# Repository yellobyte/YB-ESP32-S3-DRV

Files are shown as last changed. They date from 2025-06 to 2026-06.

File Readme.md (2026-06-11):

## YB-ESP32-S3-DRV Development Board Overview:
The **YB-ESP32-S3-DRV** is a development board based on Espressif's ESP32-S3 MCU and especially designed for driving a wide range of loads including **solenoids**, **stepper motors (e.g. 28BYJ-48)**, **high power LEDs**, etc. It features an **ESP32-S3-WROOM-1-N8R2** module (8MB Flash, 2MB PSRAM, WiFi PCB antenna) and is available on sales platforms [eBay](https://www.ebay.de/sch/i.html?_nkw=yb-esp32-s3) and [Ricardo.ch](https://www.ricardo.ch/en/s/YB-ESP32-S3).

Apart from the Espressif **ESP32-S3** MCU it provides a modern driver IC [Toshiba TBD62083A](https://github.com/yellobyte/YB-ESP32-S3-DRV/raw/main/doc/TBD62083A_datasheet.pdf) **8-channel sink type DMOS transistor array**  similar to an ULN2003/ULN2803 (7/8-channel Darlington array) but with 8 MOSFET output stages, **USB-C connector** for software upload, serial output and/or feeding power to the ESP32 section on the board, **two status LEDs** and **GPIO pins** for free use. The USB-C is connected directly to the ESP32-S3 to allow for serial output and JTAG debugging.

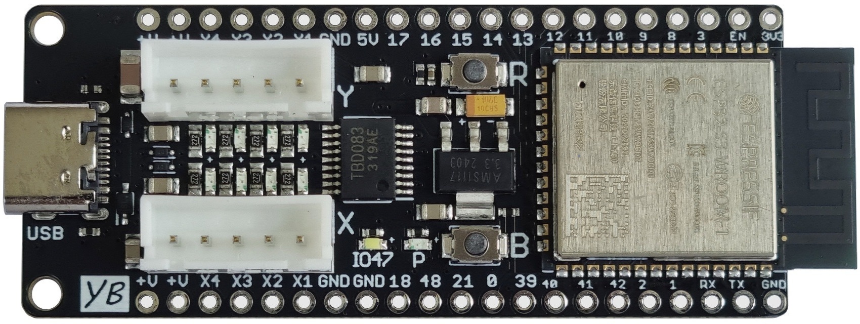
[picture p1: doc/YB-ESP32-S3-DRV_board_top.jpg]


There are plenty of GPIOs available so you can connect additional hardware to the board, e.g. TFT displays, buttons, switches, sensors, modules that communicate via I2C/SPI, etc. Please have a look at the provided [examples](https://github.com/yellobyte/YB-ESP32-S3-DRV/tree/main/examples) for PlatformIO resp. ArduinoIDE.

The densly populated 4-layer YB-ESP32-S3-DRV board is still highly [breadboard compatible](https://github.com/yellobyte/YB-ESP32-S3-DRV/raw/main/doc/YB-ESP32-S3-DRV_on_breadboard.jpg) for it leaves one row of accessible breadboard contacts on either side of the board. All I/O ports (GPIOx) are clearly labeled on both sides of the board.

### Driving inductive loads

The boards driver IC is especially suited for driving inductive loads, e.g. **solenoids** or **stepper motors**. Since a common microcontroller can only drive a few 10mA and low voltages it is commonly paired with a driver IC that can handle higher current and/or voltage levels, e.g. the very popular ULN2003/ULN2803. Such chip can drive up to 500mA current and contains suppression (flyback/freewheeling) diodes. A major disadvantage of the ULN are the darlington transistors at the output which cause a high forward voltage when switched on and therefore a considerable waste of energy. To make matters worse, the high forward voltage (Vf) of about 1.5-2V notably reduces the working voltage of a connected device.

This board features the **modern 8-channel Toshiba driver chip** with MOSFET outputs (~0.5Vf) and suppression diodes on each channel.

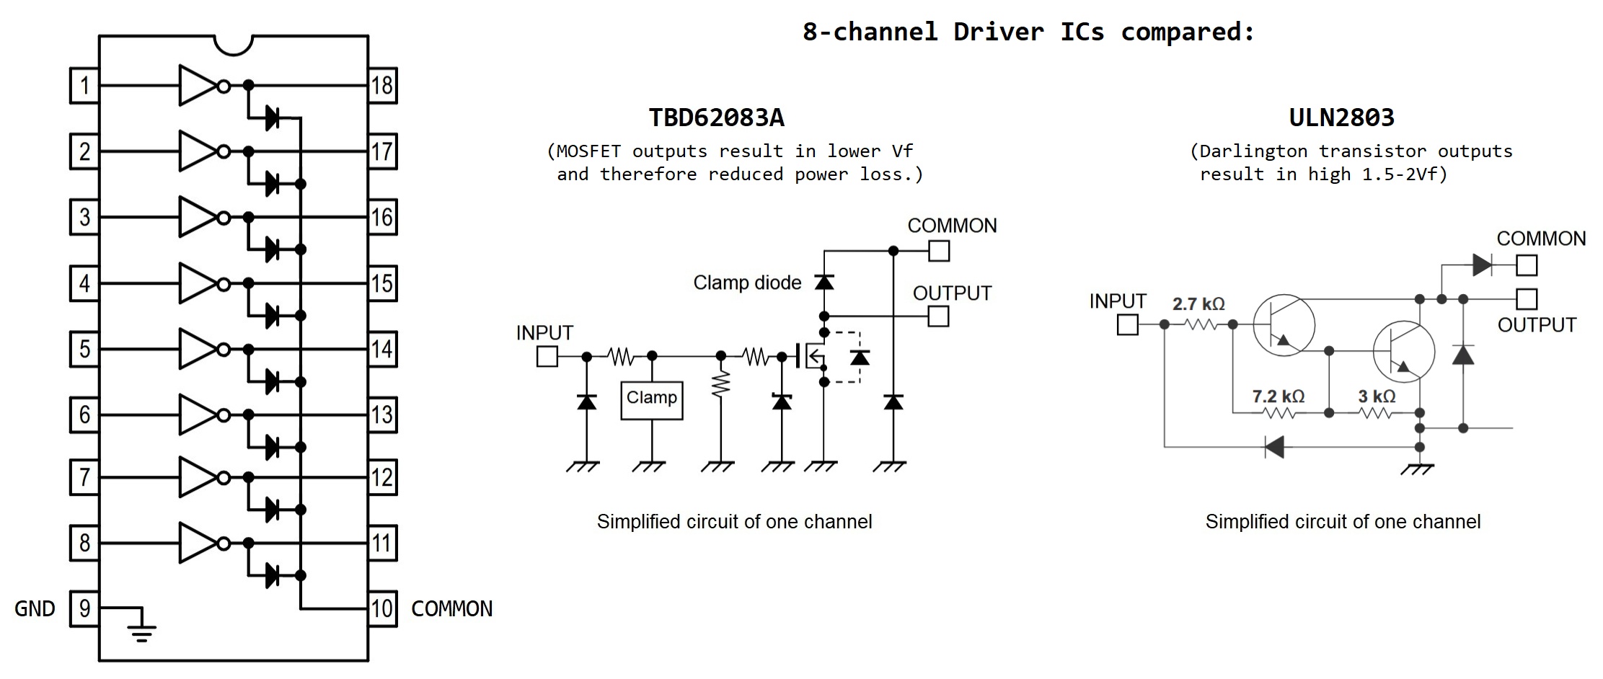
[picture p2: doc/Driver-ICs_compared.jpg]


Furthermore the board provides **two JST XH connectors** that match exactly the 5-wire connector of a common 5V/12V [**28BYJ-48 stepper motor**](https://github.com/yellobyte/YB-ESP32-S3-DRV/raw/main/doc/28BYJ-48-Stepper-Motor-Spec.pdf). This lets you easily plug two such motors into the board without the need for any extra wiring between board and steppers.

In addition, the board features **eight channel LEDs** (connected to X1...X4 and Y1...Y4) that indicate [channel activity](https://github.com/yellobyte/YB-ESP32-S3-DRV/raw/main/doc/YB-ESP32-S3-DRV_board_with_two_5V-steppers.mp4) and therefore provides a clear visual feedback as motors step or solenoids and other connected devices get activated. If you prefer them to stay dark then solder bridges LEDX/LEDY must be opened.

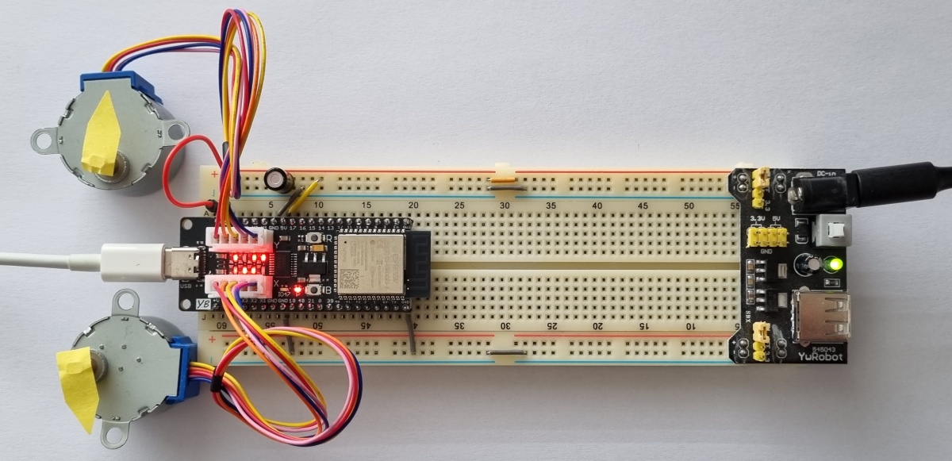
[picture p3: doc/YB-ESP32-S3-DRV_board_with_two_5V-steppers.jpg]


**Please note:**  The USB cable connected to the board in above scenario is only for data communication with a PC! The power for the two 5V stepper motors and the dev board in this case is provided by the breadboard power supply visible on the right hand side.

## YB-ESP32-S3-DRV board features in detail:
 - **ESP32-S3-WROOM-1-N8R2** module with 8MB Flash, 2MB PSRAM, WiFi PCB antenna
 - **Toshiba TBD62083A** driver IC, an 8-channel sink type DMOS transistor array with integrated suppression diodes for inductive load driving. Each channel is rated at 500mA max. output current resp. 50V max. output voltage. Outputs can be paralleled for higher current. This driver chip is similar to the commonly used ULN2803 but offers reduced forward voltage Vf at each output (when on) by using a DMOS MOSFET transistor instead of darlingtons. The chip is connected to the ESP32-S3 as follows:
   - *GPIO35...GPIO38* - for driving pins X1...X4 (additionally routed to 'X' socket)
   - *GPIO4...GPIO7* - for driving pins Y1...Y4 (additionally routed to 'Y' socket)

    Please note: The maximal power dissipation Pd of the chip must not exceed 0.96W at any time. If needed, a heat sink can be mounted on the chip. Folder [doc](https://github.com/yellobyte/YB-ESP32-S3-DRV/tree/main/doc) holds the driver IC's spec sheet.
 - **2 x JST XH connector** with 4 output channels each (connected to pins X1...X4, resp. Y1...Y4). They match exactly the 5-wire connector of a common 28BYJ-48 stepper motor.
 - **control LEDs**. One LED labeled 'P' is connected to the 3.3V rail to indicate board power and the other LED labeled 'IO47' is connected to GPIO47 which can be used as status LED.
 - **USB-C** port connected directly to the ESP32-S3 for serial output, software upload (e.g. via ArduinoIDE, VSCode/PlatformIO etc) or JTAG debugging. Can also be used to power the onboard ESP32-S3 module.

 - **Two pushbuttons**. One is labeled 'R' and resets the ESP32-S3 (shorts EN pin to ground) and the other one is labeled 'B' and shorts GPIO0 to ground when pressed. The latter is sometimes needed to force the board into boot mode.
 - **lots of available GPIOs**, useful for connecting LEDs, buttons, additional modules via SPI or I2C, e.g displays, rotary encoders, bluetooth, etc.

In summary, the board replaces a lot of separate modules & cables, saves space on a breadboard and might avoid the odd frustration to get it all running.

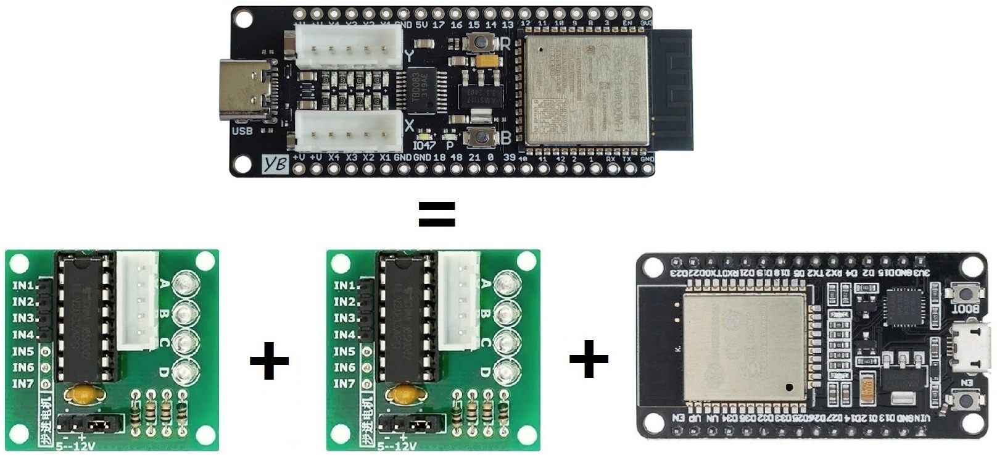
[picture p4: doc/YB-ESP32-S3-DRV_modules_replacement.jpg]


## Board Pin Layout:
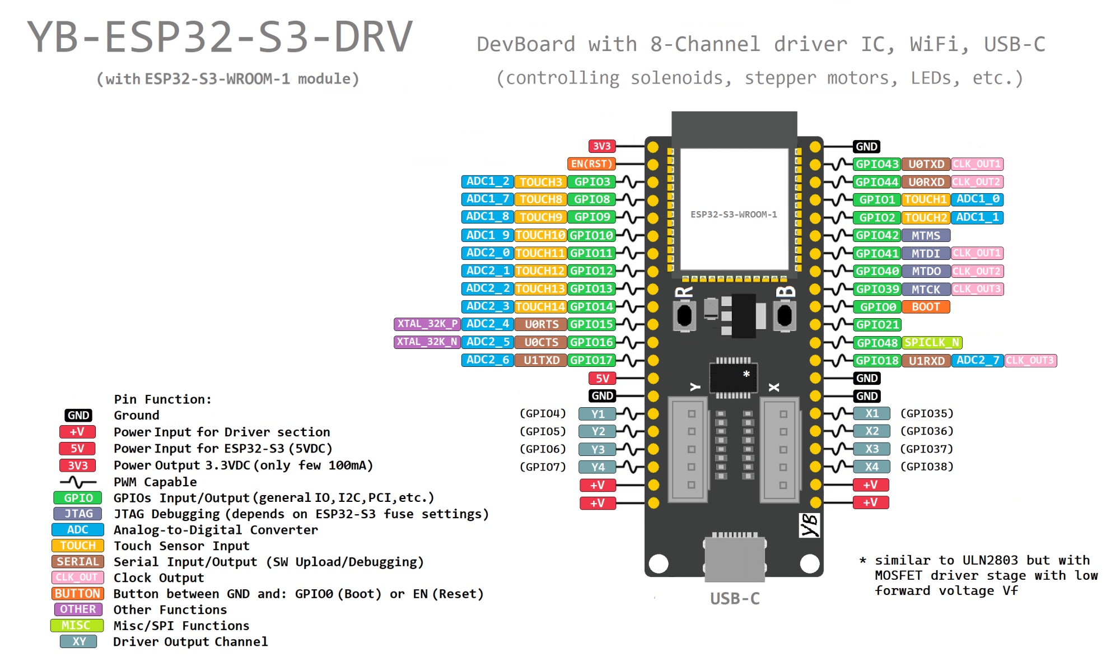
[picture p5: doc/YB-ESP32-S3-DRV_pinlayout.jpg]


The boards **pin layout**, **outline** and **schematic** files are all located in folder [doc](https://github.com/yellobyte/YB-ESP32-S3-DRV/tree/main/doc).

## Powering the board:
### ESP32 section:
There are different ways to provide power to the onboard ESP32-S3 module:
  - through the USB-C port or
  - 5VDC applied to the 5V pin

The board uses a LDO to drop the external supply voltage to 3.3Volt needed by the ESP32-S3.

### Driver section:
Board pins labeled *+V* are intended to provide power to external devices only. They are connected to pin 5 of each JST XH connector. Since all components on this +V rail (C1, C6...C9, IC1) are rated for 50Vmax you might go even higher than 12VDC if necessary.

**Important:**
You must make sure your project never exceeds the electrical and thermal limits of the driver chip IC1.

**Recommended wiring for greater loads:**
When the driver chip is supposed to carry more then just a few 10mA on each output channel than it is recommended to use a capable power supply on the +V rail and preferably an additional capacitor of 220uF or greater value across the +V/GND pins of the board as shown below:

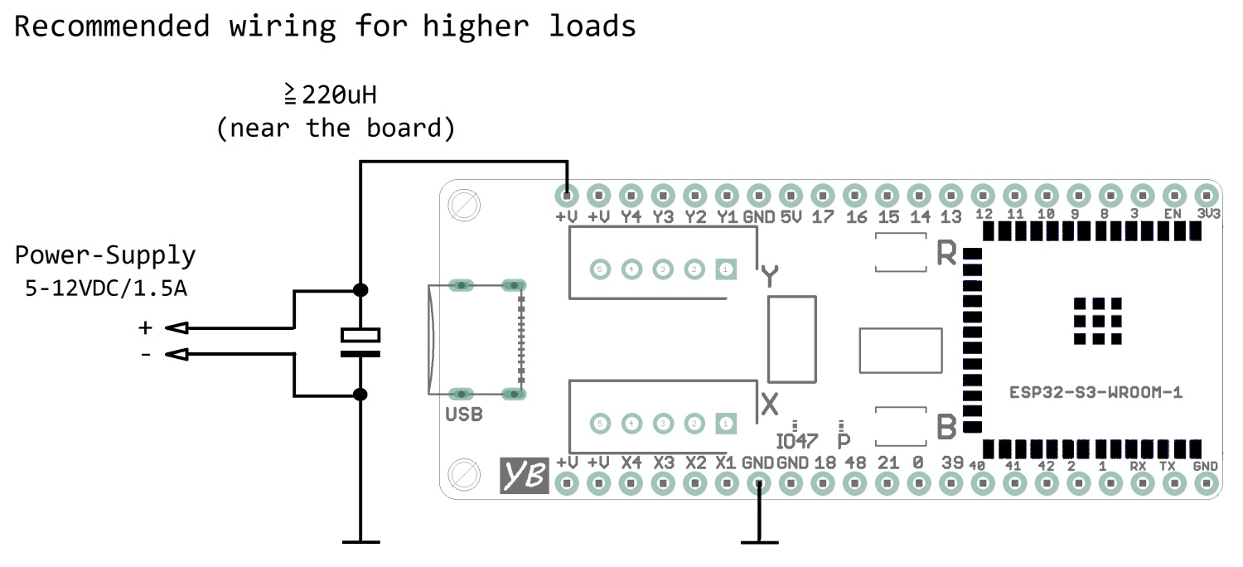
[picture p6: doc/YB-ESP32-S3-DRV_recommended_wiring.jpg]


## Application hints:

### Arduino IDE:
As of Arduino ESP32 Core V3.2.1 you open the board list, enter "yb-" and select "**Yellobyte YB-ESP32-S3-DRV**". Then choose the proper settings for COM port, debug level, flash size, PSRAM, etc. as shown below. Be aware, since the ESP32-S3 MCU is very versatile there are a lot of build options to play with. Espressif's homepage offers some help.

Correct **ArduinoIDE** settings for the **YB-ESP32-S3-DRV** board:
- Board: *YB-ESP32-S3-DRV*
- USB CDC On Boot: *Enabled*
- Flash Size: *8MB (64Mb)*
- Partition Scheme: *8MB with spiffs (...)*
- PSRAM: *QSPI PSRAM*

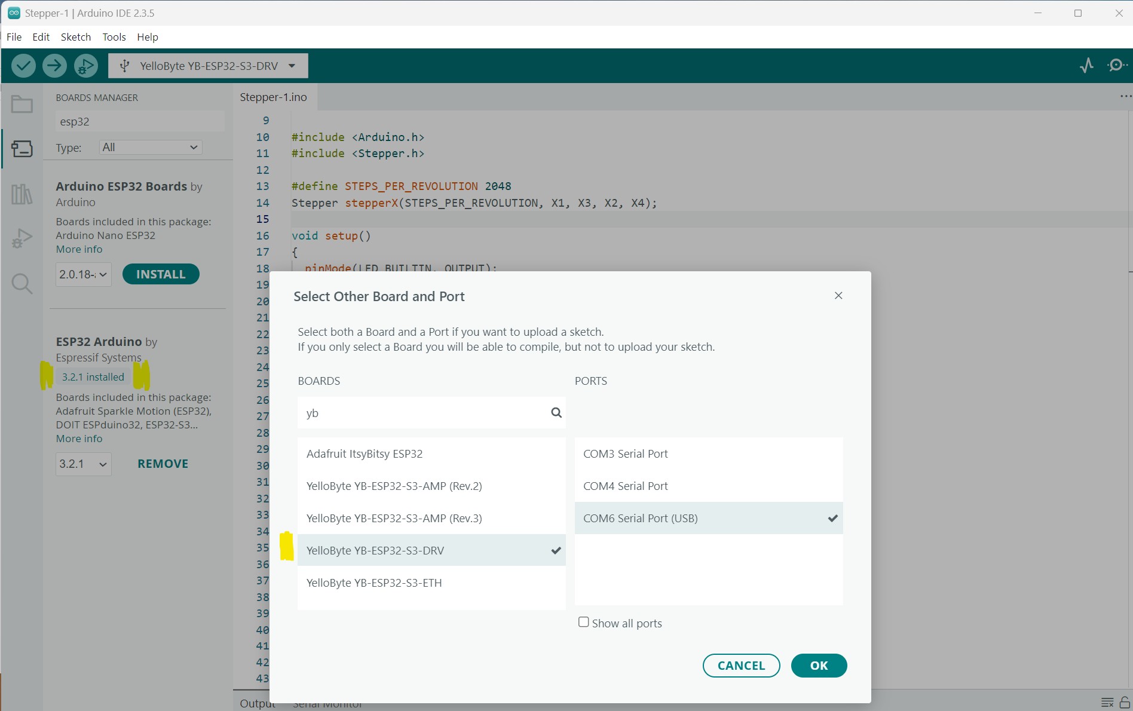
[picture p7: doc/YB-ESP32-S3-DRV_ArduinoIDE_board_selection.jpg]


### PlatformIO:
Building with **PlatformIO** is easy as well. Starting with Arduino ESP32 Core v3.3.x the VSCode/PlatformIO IDE provides the necessary variant file (pins_arduino.h) and board definition file (yb_esp32s3_drv.json).

Just create a new project, give it a name, go to board selection, enter "yb-" and finally choose the YB-ESP32-S3-DRV board from the list that's popping up.

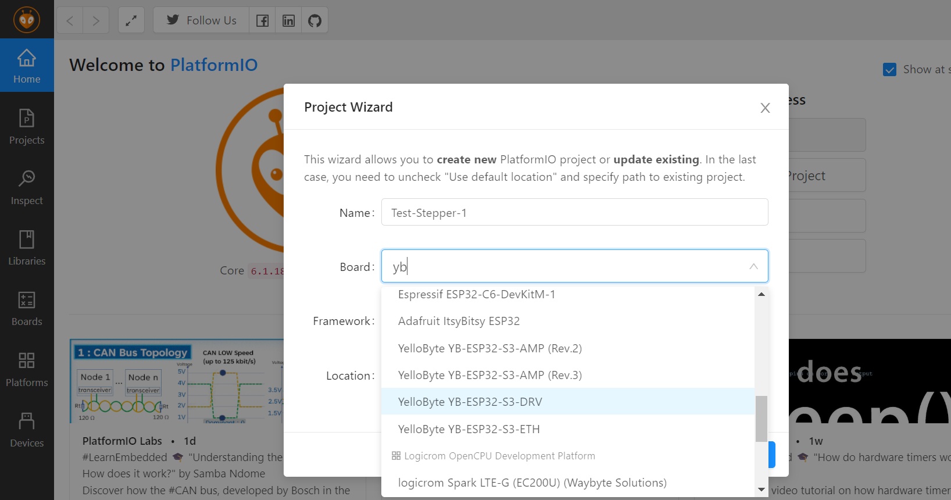
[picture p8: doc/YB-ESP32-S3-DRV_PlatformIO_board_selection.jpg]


**Note:** If you build with an older platform release and the board is missing in the board list then please copy the provided files (pins_arduino.h & yb_esp32s3_drv.json) to PlatformIO's respective folders on your PC.

### Software Upload to the board:

Uploading new software to the board with your IDE normally is a breeze. Select the correct COM port and upload the program.

However, every now and then an upload might fail and you see this:
```
ESP-ROM:esp32s3-20210327
23:10:07.248 > Build:Mar 27 2021
23:10:07.251 > rst:0x7 (TG0WDT_SYS_RST),boot:0x8 (SPI_FAST_FLASH_BOOT)
23:10:07.256 > Saved PC:0x40049087
23:10:07.256 > invalid header: 0xffffffff
23:10:07.259 > invalid header: 0xffffffff
....
```
In such case you can force the ESP32-S3 into upload mode *manually*. Keep the **'B'** button pressed, then press/release the **'R'** button and finally release the **'B'** button. The serial monitor output will subsequently confirm the boards readiness and the next upload attempt will be successful.

```
....
23:19:07.147 > invalid header: 0xffffffff
23:19:07.453 > ESP-ROM:esp32s3-20210327
23:19:07.453 > Build:Mar 27 2021
23:19:07.453 > rst:0x1 (POWERON),boot:0x0 (DOWNLOAD(USB/UART0))
23:19:07.459 > waiting for download
```

### Flash/RAM usage:

The -N8R2 module on the board should provide enough memory even for demanding projects. Building e.g. software example [Stepper-1](https://github.com/yellobyte/YB-ESP32-S3-DRV/tree/main/examples/ArduinoIDE/Stepper-1) shows the following Flash/RAM usage:
```
Executing task: C:\Users\tj\.platformio\penv\Scripts\platformio.exe run

Processing release (platform: https://github.com/pioarduino/platform-espressif32/releases/download/stable/platform-espressif32.zip; framework: arduino; board: yb_esp32s3_drv)
----------------------------------------------------------------------------------------------------------------------------------------------------------------------------------------
Verbose mode can be enabled via `-v, --verbose` option
CONFIGURATION: https://docs.platformio.org/page/boards/espressif32/yb_esp32s3_drv.html
PLATFORM: Espressif 32 (53.3.12) > YelloByte YB-ESP32-S3-DRV
HARDWARE: ESP32S3 240MHz, 320KB RAM, 8MB Flash
DEBUG: Current (cmsis-dap) External (cmsis-dap, esp-bridge, esp-builtin, esp-prog, iot-bus-jtag, jlink, minimodule, olimex-arm-usb-ocd, olimex-arm-usb-ocd-h, olimex-arm-usb-tiny-h, olimex-jtag-tiny, tumpa)
PACKAGES:
 - framework-arduinoespressif32 @ 3.1.2
 - framework-arduinoespressif32-libs @ 5.3.0+sha.489d7a2b3a
 - tool-esptoolpy @ 4.8.6
 - tool-mklittlefs @ 3.2.0
 - tool-riscv32-esp-elf-gdb @ 14.2.0+20240403
 - tool-xtensa-esp-elf-gdb @ 14.2.0+20240403
 - toolchain-riscv32-esp @ 13.2.0+20240530
 - toolchain-xtensa-esp-elf @ 13.2.0+20240530
LDF: Library Dependency Finder -> https://bit.ly/configure-pio-ldf
LDF Modes: Finder ~ chain, Compatibility ~ soft
Found 42 compatible libraries
Scanning dependencies...
Dependency Graph
|-- Stepper @ 1.1.3
Building in release mode
Retrieving maximum program size .pio\build\release\firmware.elf
Checking size .pio\build\release\firmware.elf
Advanced Memory Usage is available via "PlatformIO Home > Project Inspect"
RAM:   [=         ]   6.1% (used 20016 bytes from 327680 bytes)
Flash: [=         ]   9.2% (used 306876 bytes from 3342336 bytes)
```

## Integrating this board into your own PCB design projects:

It's easy. Folder [doc](https://github.com/yellobyte/YB-ESP32-S3-DRV/tree/main/doc) provides the necessary Eagle library file **_yb-esp32-S3-drv.lbr_** containing the boards symbol and footprint. Most other PCB design software (e.g. KiCad) are able to import and use Eagle library files.

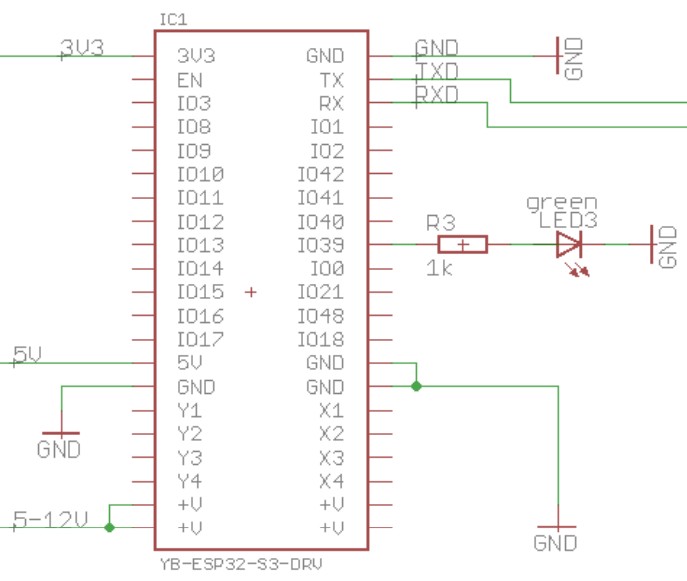
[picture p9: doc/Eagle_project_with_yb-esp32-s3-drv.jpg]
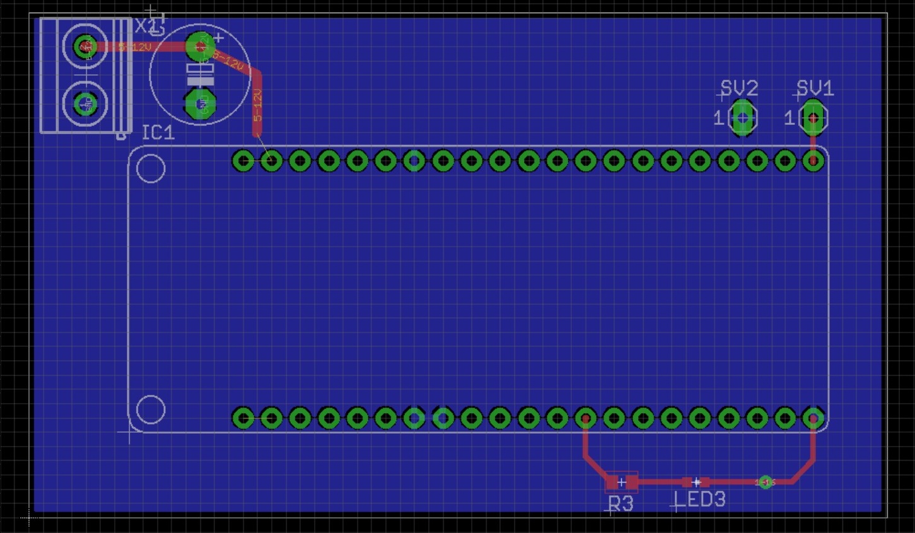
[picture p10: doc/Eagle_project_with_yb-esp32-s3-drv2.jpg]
<p align="center">&nbsp;</p>

## Integrating this board into your Fritzing projects:

It's easy. The YB-ESP32-S3-DRV board is available as custom Fritzing part (*.fzpz file) [here](https://github.com/yellobyte/YB-ESP32-S3-DRV/tree/main/examples/Fritzing). Just import the provided part file into your Fritzing application and off you go. Examples:

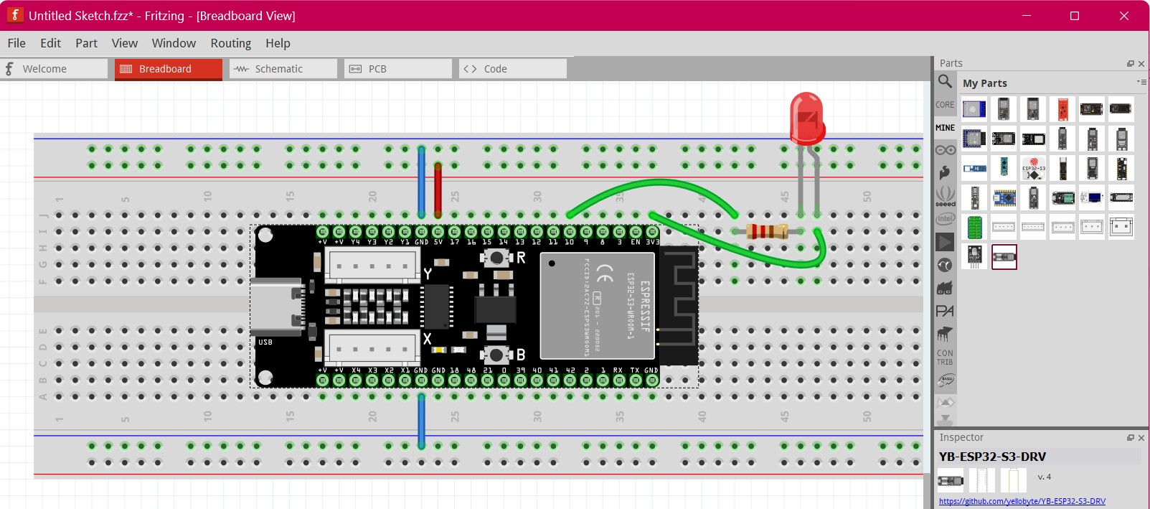
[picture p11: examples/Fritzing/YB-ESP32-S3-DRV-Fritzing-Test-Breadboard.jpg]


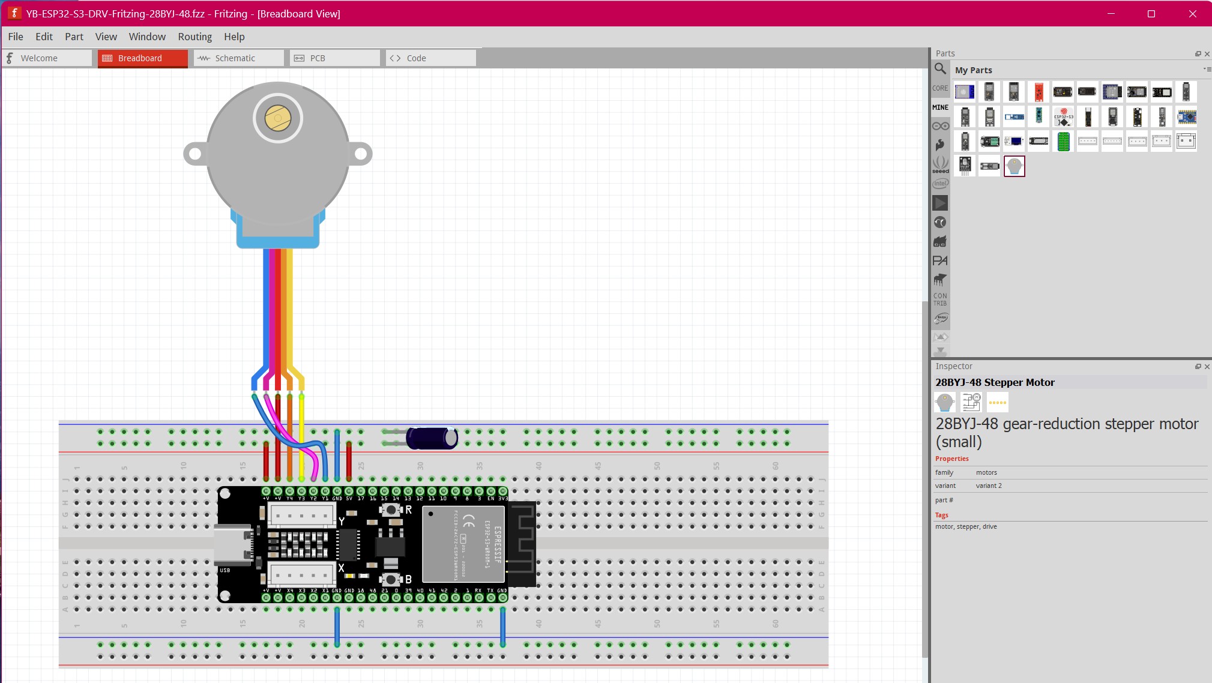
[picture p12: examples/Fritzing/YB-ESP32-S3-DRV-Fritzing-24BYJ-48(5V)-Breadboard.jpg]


## Running MicroPython on the board:

Of course you can install MicroPython onto the YB-ESP32-S3-DRV board and use it's WiFi, SPI, I2C, ADC, GPIO and other features via python scripts.  
 
**Step 1)** Load MicroPython onto the board. Go to https://micropython.org/download/ESP32_GENERIC_S3/ and download the newest *.bin firmware release. Here you will find detailed installation instructions as well.

**Step 2)** Erase the entire flash on the board with 
```
esptool.py erase_flash
```
If esptool.py can't determine which port your board is connected to, try
```
esptool.py --port PORTNAME erase_flash
```
**Step 3)** Flash the previously downloaded firmware to the board, e.g.
```
esptool.py --port COM4 --baud 460800 write_flash 0 ESP32_GENERIC_S3-20260406-v1.28.0.bin
```
**Step 4)** Reboot the board by shortly pressing the 'R' button. Then connect your serial monitor to the correct port (here COM4) and press ENTER. If flashing was successful you will be greeted with
```
01:57:53.819 > Build:Mar 27 2021
01:57:53.819 > rst:0x1 (POWERON),boot:0x8 (SPI_FAST_FLASH_BOOT)
01:57:53.825 > SPIWP:0xee
01:57:53.825 > mode:DIO, clock div:1
01:57:53.825 > load:0x3fce2820,len:0xeac
01:57:53.830 > load:0x403c8700,len:0xc28
01:57:53.830 > load:0x403cb700,len:0x2ff8
01:57:53.830 > entry 0x403c88ac
01:57:54.370 > MicroPython v1.28.0 on 2026-04-06; Generic ESP32S3 module with ESP32S3
01:57:54.375 > Type "help()" for more information.
01:57:54.375 > >>> 
```
which confirms that MicroPython is now up and running on your board. Just enter *help()* and MicroPython will present some help info.

**Example: Switching the onboard status LED (GPIO47) on/off:**
```
>>> import machine <Enter>
>>> from machine import Pin <Enter>
>>> p0 = Pin(47, Pin.OUT) <Enter>
>>> p0.on() <Enter>
>>> p0.off() <Enter>
```
<!--## Final Remark:  -->

## General notes:

1) The ESP32-S3-WROOM-1 module family comprises several [**versions**](https://github.com/yellobyte/ESP32-DevBoards-Getting-Started/raw/main/ESP32_specs_and_manuals/ESP32-S3-WROOM-1(U)_Variants.jpg). The **-1** versions come with embedded PCB antenna, the **-1U** versions with IPEX antenna socket instead. The extension -Nx(Ry) defines the amount of integrated FLASH/PSRAM, e.g. -N4 (4MB Flash, no PSRAM), -N4R2 (4 MB Flash, 2MB PSRAM), -N8R2 (8 MB Flash, 2MB PSRAM) etc.

2) The board supports USB Serial JTAG debugging. An example is provided [here](https://github.com/yellobyte/YB-ESP32-S3-DRV/tree/main/examples/PlatformIO/Debug-via-builtin-JTAG).

3) If you want to learn more about stepper motors in general and how to drive them please have a look at the following very informative websites:
https://randomnerdtutorials.com/stepper-motor-esp32-web-server/
https://www.instructables.com/Controlling-a-Stepper-Motor-with-an-Arduino/
https://www.instructables.com/How-to-Control-28BYJ-48-Stepper-Motor-With-ULN2003/
https://lastminuteengineers.com/28byj48-stepper-motor-arduino-tutorial/

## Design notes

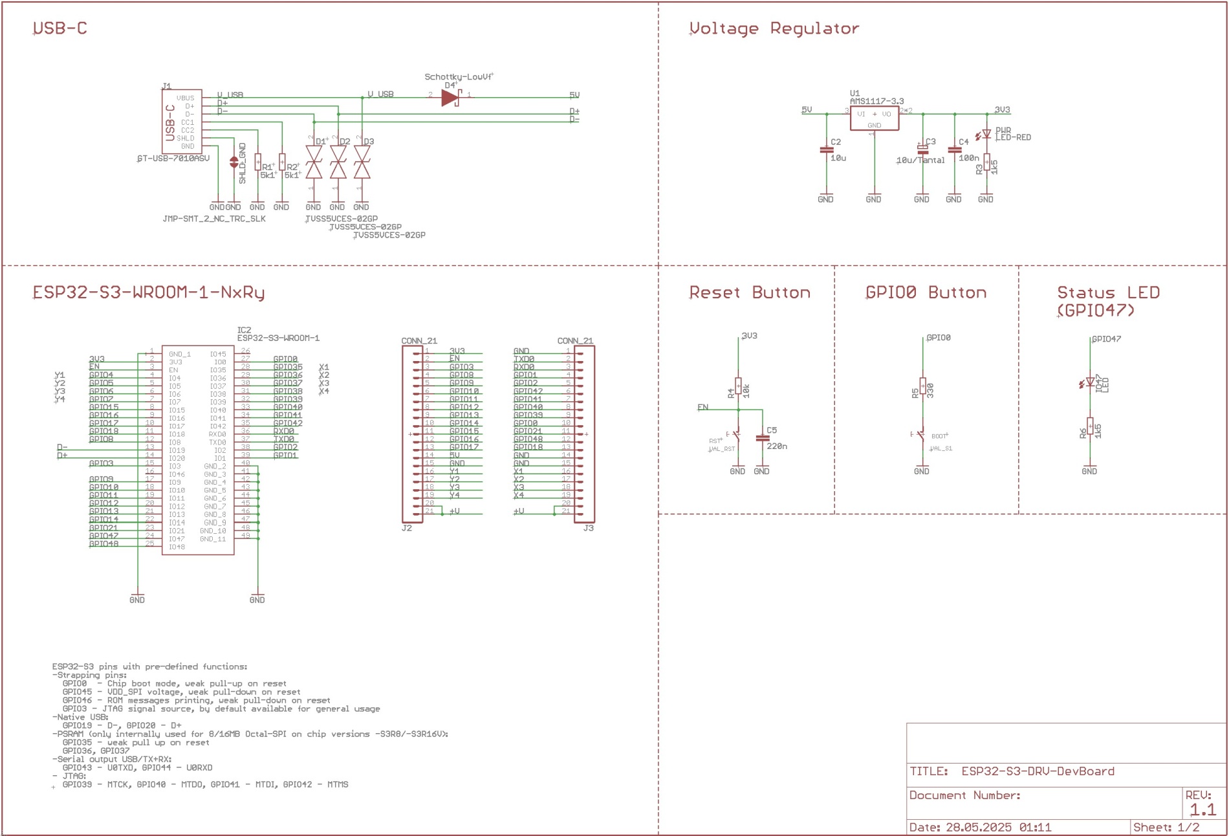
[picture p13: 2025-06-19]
doc/YB-ESP32-S3-DRV_schematic_1_2.jpg

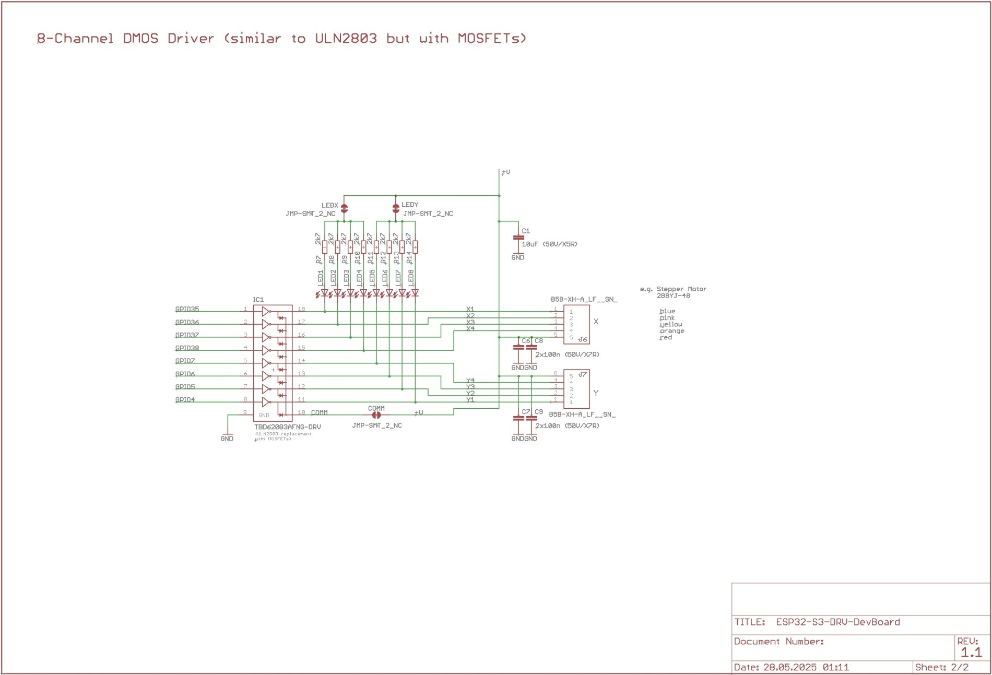
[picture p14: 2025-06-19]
doc/YB-ESP32-S3-DRV_schematic_2_2.jpg

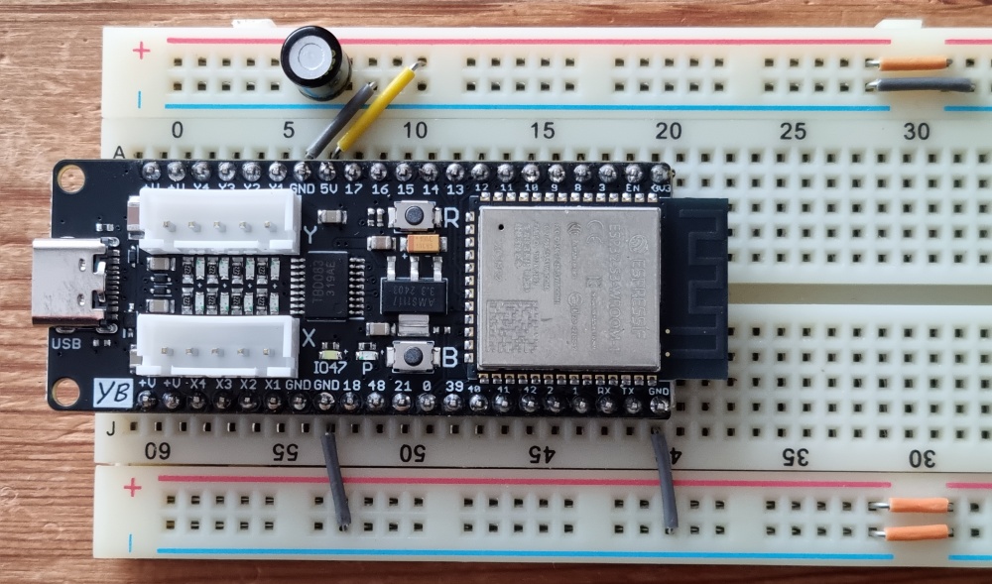
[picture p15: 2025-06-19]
doc/YB-ESP32-S3-DRV_on_breadboard.jpg

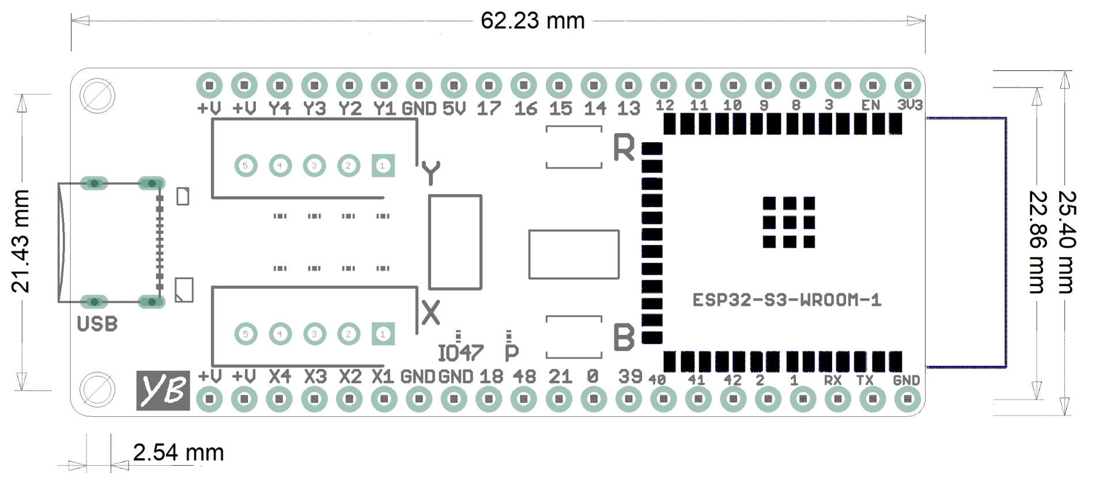
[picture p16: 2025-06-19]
doc/YB-ESP32-S3-DRV_outline.jpg

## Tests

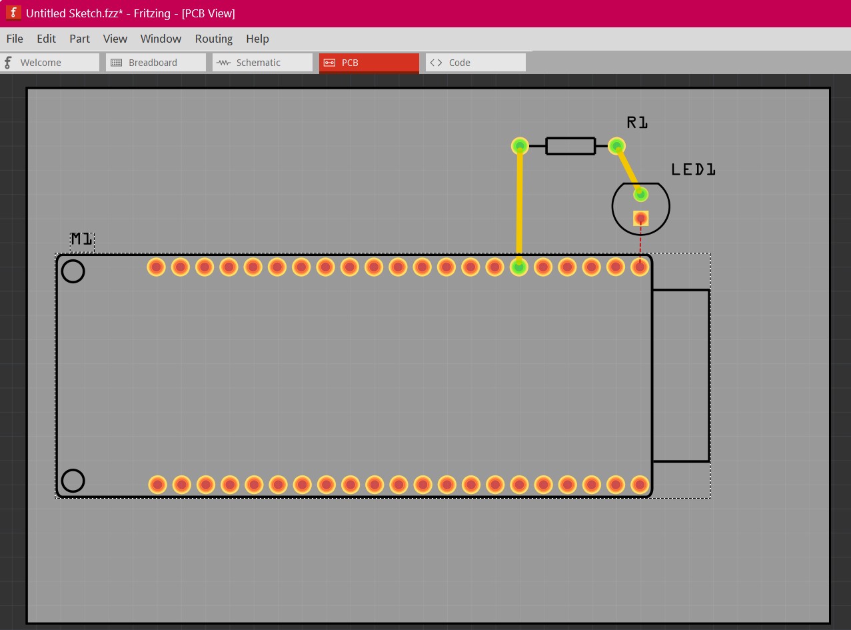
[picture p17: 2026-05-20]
examples/Fritzing/YB-ESP32-S3-DRV-Fritzing-Test-PCB.jpg

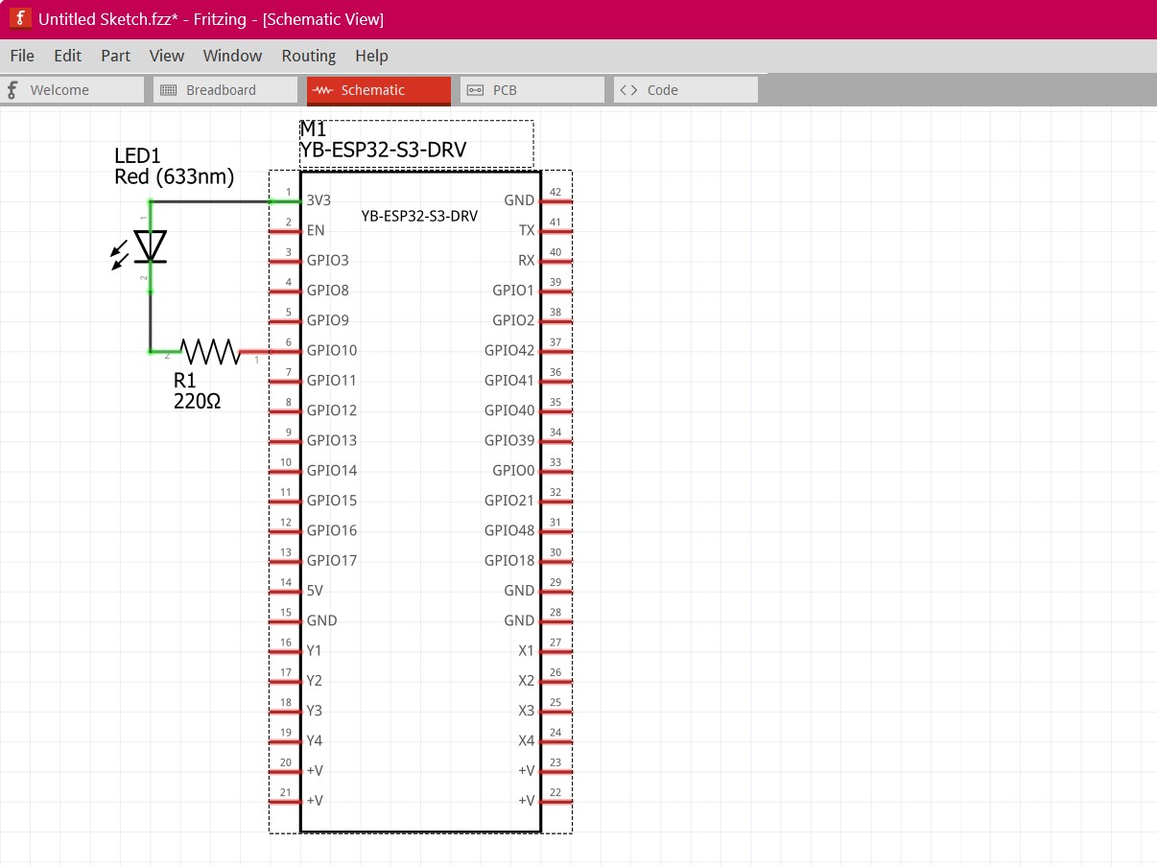
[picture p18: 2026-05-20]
examples/Fritzing/YB-ESP32-S3-DRV-Fritzing-Test-Schematic.jpg

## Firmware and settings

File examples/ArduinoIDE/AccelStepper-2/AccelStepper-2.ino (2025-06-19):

/*
  AccelStepper-2

  Controls 2 stepper motors of common type 28BYJ-48 attached to connectors X and Y.
  The motor on connector X will rotate 180° only, the other one on Y a full 360°.
  
  Last updated 2025-05-21, ThJ <yellobyte@bluewin.ch>
*/

#include <Arduino.h>
#include <AccelStepper.h>

unsigned long now, last = millis();
AccelStepper stepperX(AccelStepper::HALF4WIRE, X1, X3, X2, X4);
AccelStepper stepperY(AccelStepper::FULL4WIRE, Y1, Y3, Y2, Y4);

void setup()
{
  pinMode(LED_BUILTIN, OUTPUT);
  digitalWrite(LED_BUILTIN, LOW);          // status LED off

  Serial.begin(115200);
#if ARDUINO_USB_CDC_ON_BOOT == 1
  // only continue when serial port becomes available
  while (!Serial);
#endif  
  delay(2000);
  Serial.println();
  Serial.println("running example \"AccelStepper-2\"");

  stepperX.setMaxSpeed(1000.0);
  stepperX.setAcceleration(200.0);
  stepperX.setSpeed(200);
  stepperX.moveTo(1024);  // start clockwise

  stepperY.setMaxSpeed(1000.0);
  stepperY.setAcceleration(50.0);
  stepperY.setSpeed(200);
  stepperY.moveTo(-1024);  // start counterclockwise
}

void loop()
{
  // every 250ms the actual status gets printed 
  now = millis();
  if ((now - last) >= 250) {
    last = now;
    Serial.printf("X: pos=%d, dist=%d, speed=%d\n", 
                  stepperX.currentPosition(), stepperX.distanceToGo(), (int)stepperX.speed());
    Serial.printf("Y: pos=%d, dist=%d, speed=%d\n", 
                  stepperY.currentPosition(), stepperY.distanceToGo(), (int)stepperY.speed());
  }

  // change direction when motor reaches target position
  if (stepperX.distanceToGo() == 0) {
    Serial.println("X: dist=0, change of direction...");
    digitalWrite(LED_BUILTIN, !digitalRead(LED_BUILTIN));
    stepperX.moveTo(-stepperX.currentPosition());
  }
  if (stepperY.distanceToGo() == 0) {
    Serial.println("Y: dist=0, change of direction...");
    stepperY.moveTo(-stepperY.currentPosition());
  }

  // move each motor one step
  stepperX.run();
  stepperY.run();
}
